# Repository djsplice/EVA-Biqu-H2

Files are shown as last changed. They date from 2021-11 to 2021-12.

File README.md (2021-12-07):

# EVA mount for the Biqu H2 hot end / extruder

These were designed to work with the [Mercury One](https://github.com/ZeroGDesign/Mercury) conversion for an Ender 5. Rudra has made an [EVA universal faceplate](https://drive.google.com/drive/folders/1WeMnU41LHNeeJy4bnJhXC6Zqy8RPeaLE) based on the EVA v2 spec that works with the Mercury One belt paths.

This is a mount that connects the Biqu H2 hot end and extruder to the EVA Mercury faceplate, with fan duct to match. I've recently switched over to a dual 5015 fan configuration which required some updates to the fan duct. I decided to keep both versions in case people want to use one over the other.

### Single 5015 configuration
Use the EVA-Biqu-H2-Fan_Duct.stl for a single 5015 fan setup, it will work with the standard EVA bottom mount.

### Dual 5015 configuration
Use the EVA-Biqu-H2-Fan_Duct-Dual_5015.stl for a dual 5015 fan setup. You will need to print the [Dual 5015 Part Fan MGN12 Wide Bottom](https://contrib.eva-3d.page/cooling/assets/dual_5015_bottom_mgn12_wide.stp) based on [SuperSniffles' Dual 5015 Part Fan Mod](https://contrib.eva-3d.page/cooling/dual_5015_part_fan/) and the [Dual 5015 Back](https://cad.onshape.com/documents/3150483a4a0db74e9c812414/w/fabd97c377670e0877f4f9b6/e/330a36823247faf38c00b828), as of now still in beta - designed to work with the MercuryOne made by Rudra.

The fan duct is loosely based on the official [EVA](https://main.eva-3d.page/) fan ducts. 'Loosely' in the fact that I'm a CAD n00b, and the official designs have much more thought/testing put into them compared to my functional yet hacky rendtion! ;)

Big thanks to all the designers of EVA and associated mods, great work!

## Images
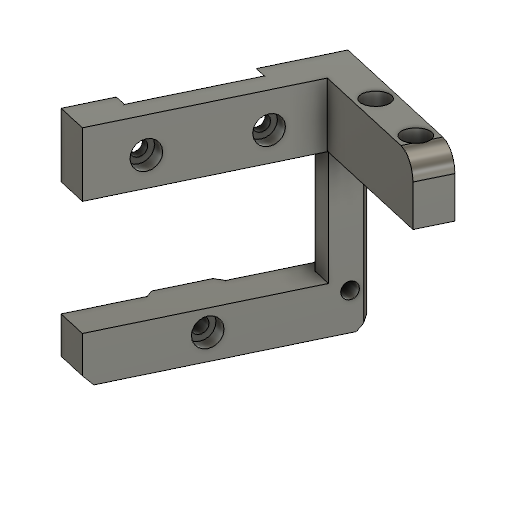
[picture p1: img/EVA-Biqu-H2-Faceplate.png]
Face Plate

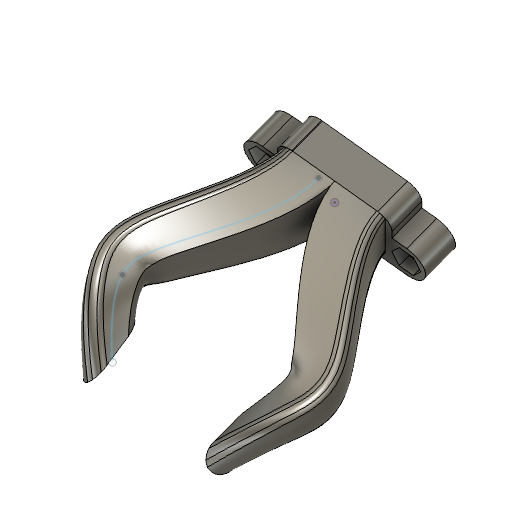
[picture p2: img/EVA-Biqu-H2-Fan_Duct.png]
Fan Duct


## Installation
* Download and print [EVA universal faceplate](https://drive.google.com/drive/folders/1WeMnU41LHNeeJy4bnJhXC6Zqy8RPeaLE), the Eva Biqu H2 mount, and the Fan duct.

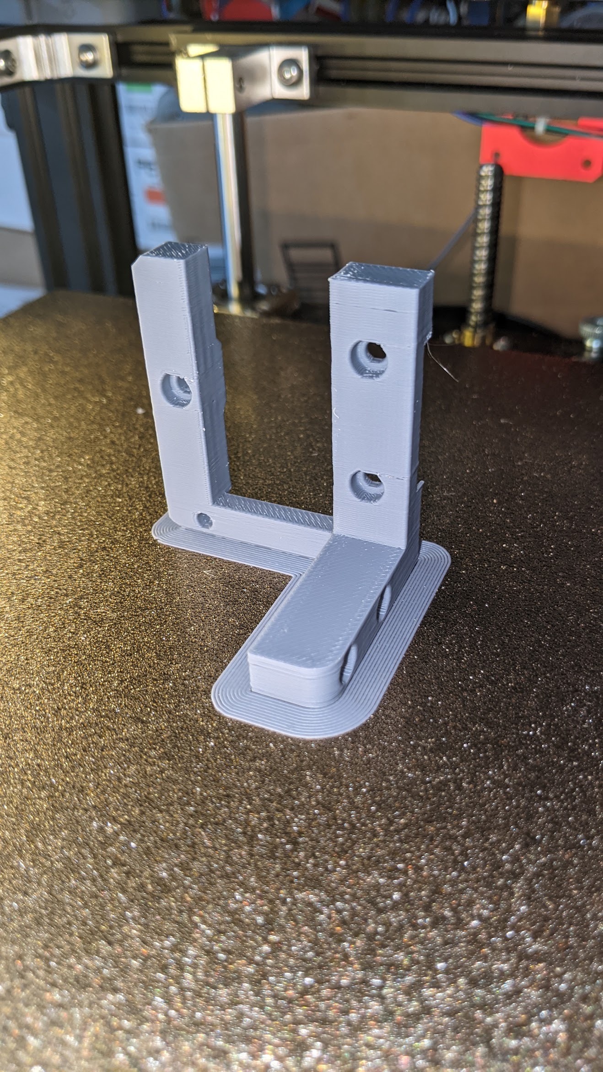
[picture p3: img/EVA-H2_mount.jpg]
Print orientation H2 Mount


* Attach the H2 faceplate to the EVA carriage using 3 M3 screws
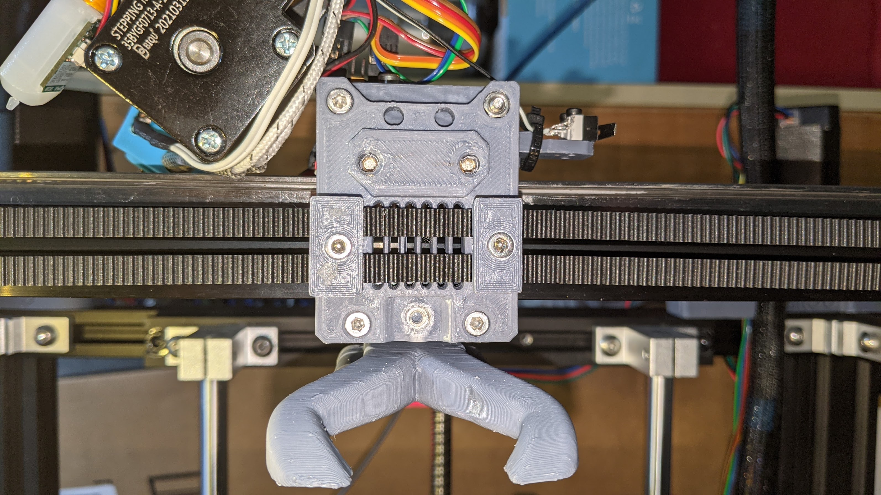
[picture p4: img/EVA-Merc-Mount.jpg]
EVA - Merc mount


* Attach the fan duct to the EVA carriage

* Attach the H2 to the faceplate via 2 screws on top of the H2, and one screw in the back.

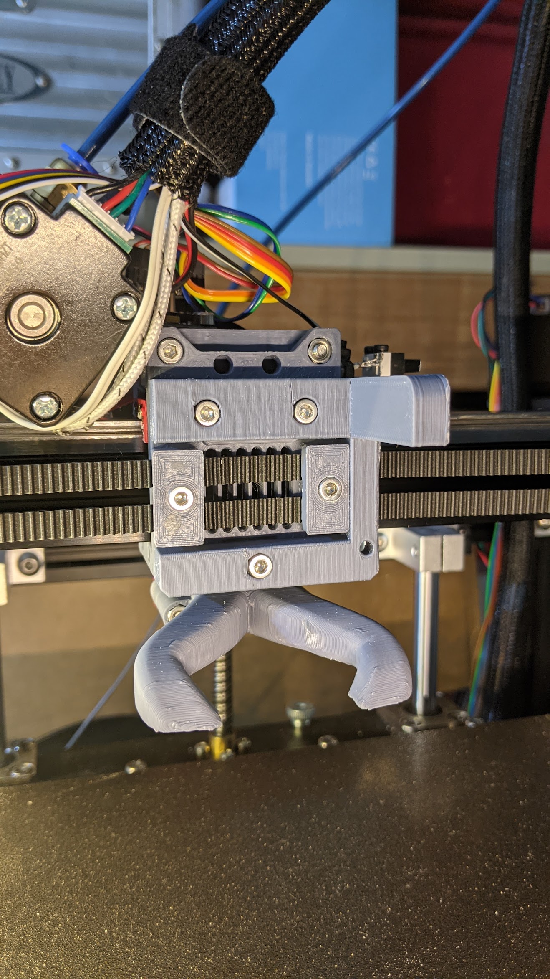
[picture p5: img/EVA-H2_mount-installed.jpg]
Merc - H2 Faceplate mounted

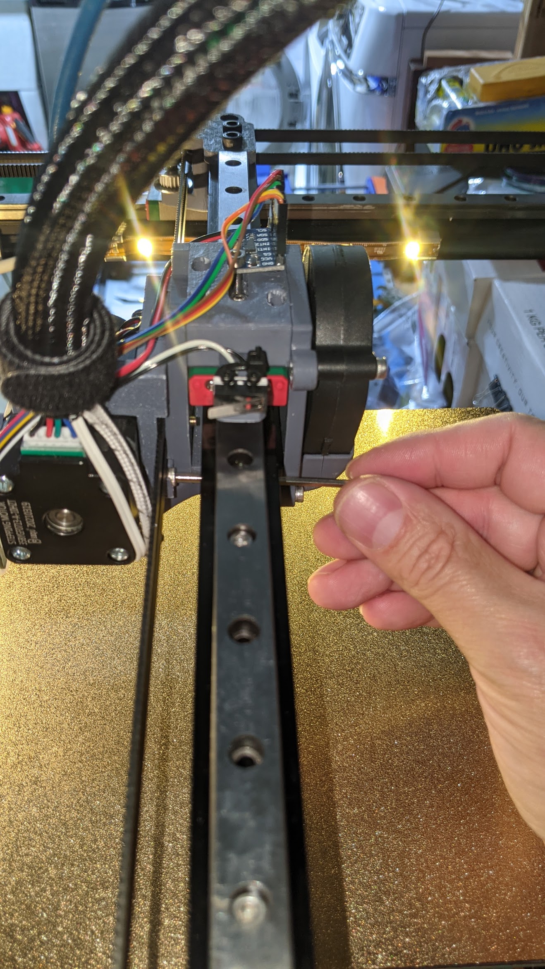
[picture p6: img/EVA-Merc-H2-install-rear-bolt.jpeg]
Merc - H2 rear bolt


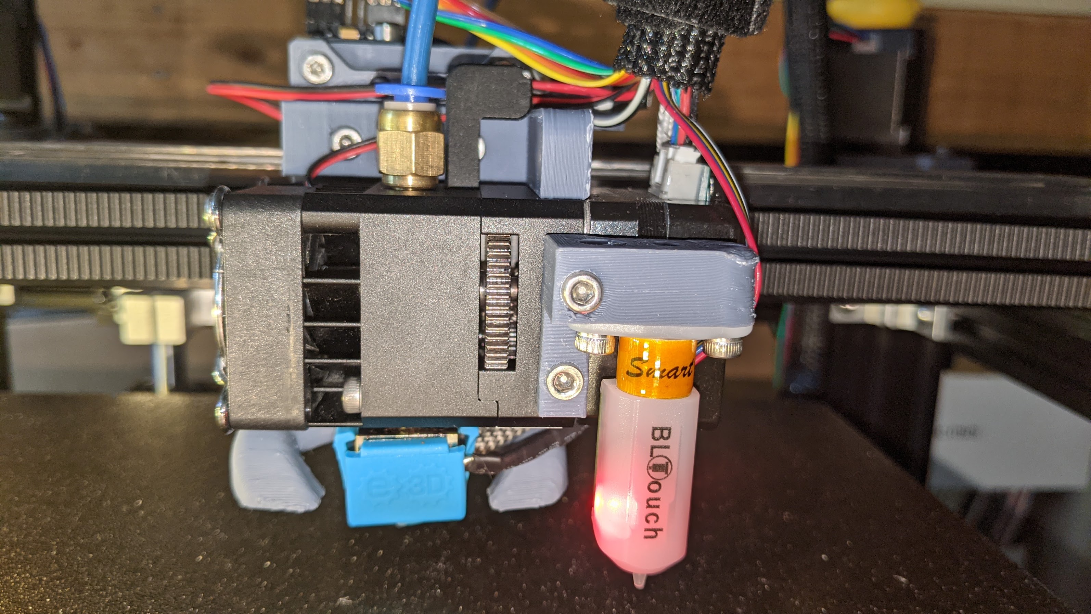
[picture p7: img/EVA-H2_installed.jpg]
Installed


## Known Issues
1. I optimized the design to make it fairly easy to remove the H2 from the EVA carriage while providing good rigidity using 3 point connections (3 screws between the faceplate and the carriage, and 3 screws connecting the H2 to the faceplate). In initial iterations of this design, I'd tried connecting the H2 to the faceplate using only two screws, but vibrations at higher print speeds had negative effects on quality.

2. Because of the challenges with bolt clearances between the H2 mounts and the faceplate, the extruder is ever so slightly off center from the carriage. It's about 2mm off of center from the carriage which slightly interferes with the fan duct.

3. I had to design a new fan duct because existing mods didn't quite fit correctly for me. The current nozzle design sits pretty close to the build plate, 1mm clearance. Because of the H2 / carriage offset, the right side air duct seems to be a bit impeded. While there's more optimization to be had here, the fan duct works pretty well for general purpose prints.

4. I'm a CAD n000b - I make things that work for me, and by sharing them I hope others find utility in them as well!

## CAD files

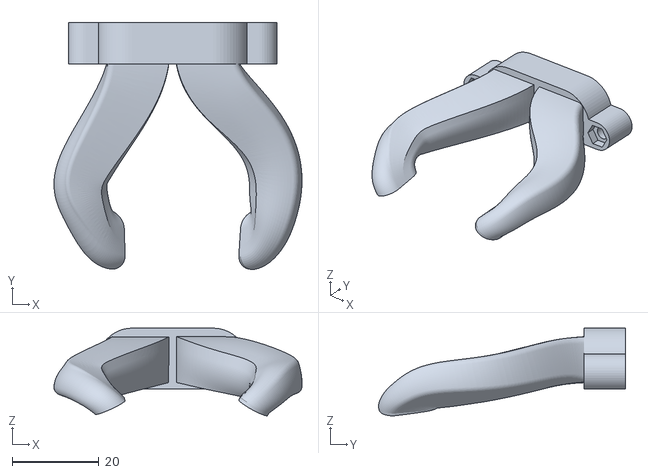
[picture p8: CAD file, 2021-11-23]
EVA-Biqu-H2-Fan_Duct-Dual_5015.stl
57.0 x 56.8 x 20.2

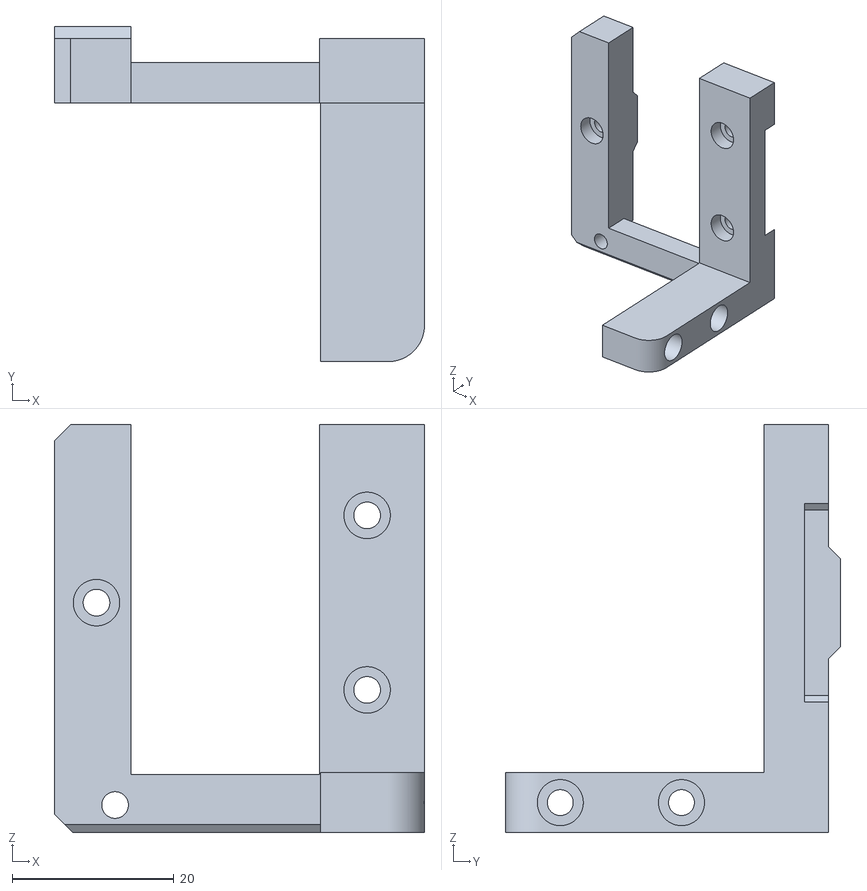
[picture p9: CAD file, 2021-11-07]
EVA-Biqu-H2-Faceplate.stl
45.8 x 41.5 x 50.5

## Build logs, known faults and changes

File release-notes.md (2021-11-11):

# Release Notes

## v0.2.0 - November 11, 2021
* Updated the fan duct to provide better bed/part clearance
* Updated the fan duct to focus air flow more directly over the hot end nozzle
* Updated fan duct image
* Readme updates

## v0.1.0 - November 9, 2021
* Initial commit of mounting bracket for EVA / Biqu H2
* Initial commit of fan duct for EVA / Biqu H2

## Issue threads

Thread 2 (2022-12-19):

Bottom section for narrower fan duct

smwoodward, 2022-12-19:
Do you have the STL for the bottom section of the EVA that will fit the fan duct?  I was able to find the back plate that is narrower to fit the fan duct, but not the bottom plate.

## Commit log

2021-11-07 Adding STLs
    [EVA-Biqu-H2-Faceplate.stl]
2021-11-09 Updated fan duct. Increased bed clearance by 1mm and repositioned nozzle output for better cooling
2021-11-11 Updated fan duct - more clearance from the bed, better focus of airflow
2021-11-11 Updated Fan Duct picture
2021-11-13 Moved nozzle back for better focus of airlfow, moved right duct away from the hotend for better airflow
2021-11-23 Adding support for a dual 5015 fan configuration
    [EVA-Biqu-H2-Fan_Duct-Dual_5015.stl]
